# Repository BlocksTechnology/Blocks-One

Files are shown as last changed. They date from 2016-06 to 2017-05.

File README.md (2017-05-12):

# Blocks one
In this repository you will find the firmware source code, BOM, STLs of the printed parts and frames for the [Blocks one 3D printer](http://blockstec.com/one.html)

# Updating the firmware:
 - Download and install Cura 15.02.1: [Win](http://software.ultimaker.com/old/Cura_15.02.1.exe) / [Mac](http://software.ultimaker.com/old/Cura-15.02.1-MacOS.dmg)
 - Download the [HEX file](http://blockstec.com/downloads/Blocks_one_1.2.hex)
 - Connect your USB printer cable
 - Open Cura and select menu "Machine" -> "Install custom firmware"
 - Select the downloaded HEX file.
 - Wait for the upload to finish and press "OK"

In case the update does not start, please verify the "Serial port" and "Baudrate" (250000) settings in the menu "Machine" -> "Machine settings".

# Changelog:
V1.2.1:
 - Homing after print bug solved

V1.2:
 - USB communication bug solved
 - Baudrate changed to 250000

V1.1:
 - New load/unload filament routine
 - Option to clean the nozzle before bed level
 - Thermal runaway safety feature
 - Filament runout (needs printing new extruder and adding a microswitch to work)
 - Reversed direction of the LCD knob

# License
Blocks one is licensed under a [Creative Commons Attribution-ShareAlike 4.0 International License](http://creativecommons.org/licenses/by-sa/4.0/)

# Firmware
The firmware was based on [Marlin](https://github.com/MarlinFirmware/Marlin) and https://github.com/bq/Marlin

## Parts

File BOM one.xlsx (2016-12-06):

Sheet: Blocks One
Item | Quantidade | Dimensões
Acrilico Opalino | 6 | (5mm) 41 x 41cm
Peças Impressas | 20 | zzz
Motores | 4 | Nema 17
Hotend | 1 | zzz
Tira Led | 1 | zzz
Blower | 1 | 50x50x15
Fan | 1 | 30x30x10
Fan | 1 | 50x50x10
Belt GT2 | 3 | 3m
Pulley GT2 | 2 | 6mm
Idler | 8 | 8mm
Fitting | 2 | 4mm
PTFE | 1 | 60cm
Endstop | 3 | 12x6mm
Pinhão Extrusor | 1 | 1.75
Molas Fortes | 2 | zzz
Molas Suaves | 4 | zzz
Varões M8 | 4 | 39cm
Varões M10 | 2 | 39cm
Lead Screw M8 | 1 | 33cm
Rolamento LM8UU | 8 | zzz
Rolamento LM10UU | 4 | zzz
Rolamento 608ZZ | 3 | zzz
Coupling M5/M8 | 1 | zzz
HeatedBed | 1 | zzz
Pwr Supply | 1 | zzz
Arduino Mega 2560 | 1 | zzz
Ramps 1.4 | 1 | zzz
Pololu Drivers | 4 | zzz
LCD Smart Discount | 1 | zzz
Cabo Elect | 1 | zzz
Guia Cabo | 1 | zzz
Int. 220v | 1 | zzz
Cabo Pwr | 1 | zzz
Total

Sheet: REV
Item | QT | Dimensions | Supplier
ACRILIC | 6 | 410x410x5mm
PRINTED PARTS | 35
LEDS STRIP | 1 | 30 mm
BLOWER FAN | 2 |  | http://ledsandchips.com/3DPrinter/Electronics/504
FAN 30X30 | 1 |  | http://ledsandchips.com/3DPrinter/Electronics/470
GT2 BELT | 2 | 125 mm | http://ledsandchips.com/3DPrinter/3DPrinter_Mechanics/328
GT2 PULLEY | 2 |  | http://ledsandchips.com/3DPrinter/3DPrinter_Mechanics/549
IDLER PULLEY | 8 |  | http://ledsandchips.com/3DPrinter/3DPrinter_Mechanics/557
625-2RS Ball Bearing | 16 |  | http://ledsandchips.com/3DPrinter/3DPrinter_Mechanics/550
NICKEL SPACER M5 | 4 | 10mm | http://ledsandchips.com/3DPrinter/3DPrinter_Mechanics/587-2
FITING PTFE | 2 |  | http://ledsandchips.com/3DPrinter/Extruder_HotEnd/463
PTFE TUBE | 1 | 600 mm | http://ledsandchips.com/3DPrinter/Extruder_HotEnd/463
MICROSWITCH | 3 |  | http://ledsandchips.com/080?search=microswitch
MK7 EXTRUDER PIN | 1 |  | http://ledsandchips.com/3DPrinter/Extruder_HotEnd/506
STRONG SPRINGS | 2 | 20mm | https://reprapworld.com/products/mechanical/compression_springs/compression_spring_20mm_od_5mm/
SOFT SPRINGS | 4 | 12mm | http://reprap.pt/pecas/molas
VARÕES M8 | 4 | 380 mm | http://reprap.pt/pecas/varao-liso-ao-metro
VARÔES M10 | 2 | 350 mm | http://reprap.pt/pecas/varao-liso-ao-metro
LEAD SCREW | 1 | 300 mm | http://reprap.pt/pecas/varao-roscado-8mm-dia-por-350mm-comp-com-parafuso
LM8UU | 8 |  | http://ledsandchips.com/3DPrinter/3DPrinter_Mechanics/176
LM10UU | 4 |  | http://ledsandchips.com/3DPrinter/3DPrinter_Mechanics/284
608ZZ Ball Bearing | 1 |  | http://ledsandchips.com/3DPrinter/3DPrinter_Mechanics/368
COUPLING M5/M8 | 1 |  | http://ledsandchips.com/3DPrinter/3DPrinter_Mechanics/299
NEMA17 2.5A | 4 |  | http://ledsandchips.com/Motors/604
HOTEND | 1 |  | Hotend (https://pt.aliexpress.com/item/3D-Printer-E3DV6-Kits-Remote-Long-Distance-Sprinkler-head-Heating-Print-Head-Extruder-Extrusion-head-Heating/32455907727.html)
HEATEDBED | 1 |  | http://www.cubic-print.com/MK3-aluminum
NTC TERMISTOR | 1 |  | http://ledsandchips.com/3DPrinter/Extruder_HotEnd/350
POWER SUPPLY 12v 25A | 1 |  | http://ledsandchips.com/3DPrinter/Electronics/420
ARDUINO MEGA 2560 | 1 |  | http://ledsandchips.com/Arduino/011
RAMPS 1.4 | 1 |  | http://ledsandchips.com/3DPrinter/Electronics/218
POLULO DRIVERS | 4 |  | http://ledsandchips.com/Motors/560
LCD S.DISCOUNT | 1 |  | http://ledsandchips.com/3DPrinter/Electronics/373
CABLE 220V | 1 |  | https://mauser.pt/catalog/product_info.php?cPath=1874_57_331&products_id=76002
CABLE GUIDE | 1 |  | http://www.tme.eu/en/details/cyg-pet-15-bk/polyester-conduits/cyg/cyg-pet15/
POWER PLUG 10A | 1 |  | https://mauser.pt/catalog/product_info.php?cPath=1874_640_1107&products_id=61780
SWITCH 220V | 1 |  | https://mauser.pt/catalog/product_info.php?cPath=324_1401_1402&products_id=66105
GLASS PLATE | 1 | 215x215x3 mm
Screws Nuts & washers
M3 SCREW 10mm | 15
M3 SCREW M3 16mm | 20
M3 SCREW 20mm | 8
M3 SCREW 30mm | 20
M3 SCREW 40mm | 20
M3 SCREW 50mm | 4
M4 SCREW 16mm | 72
M4 SCREW 20mm | 12
M4 SCREW 50mm | 2
M5 SCREW 30mm | 2
M5 SCREW 35mm | 2
M5 SCREW 40mm | 2
M5 SCREW 45mm | 2
M3 NUT | 25
M4 NUT | 120
M5 NUT (SELF TIGHTENING) | 8
M5 WASHER | 8 | 10x1 mm

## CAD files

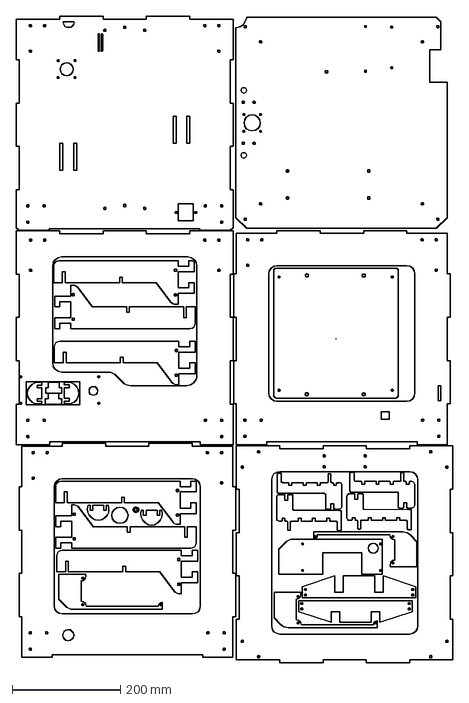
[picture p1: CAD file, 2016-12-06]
frames laser.DXF
806.9 x 1193.1 mm

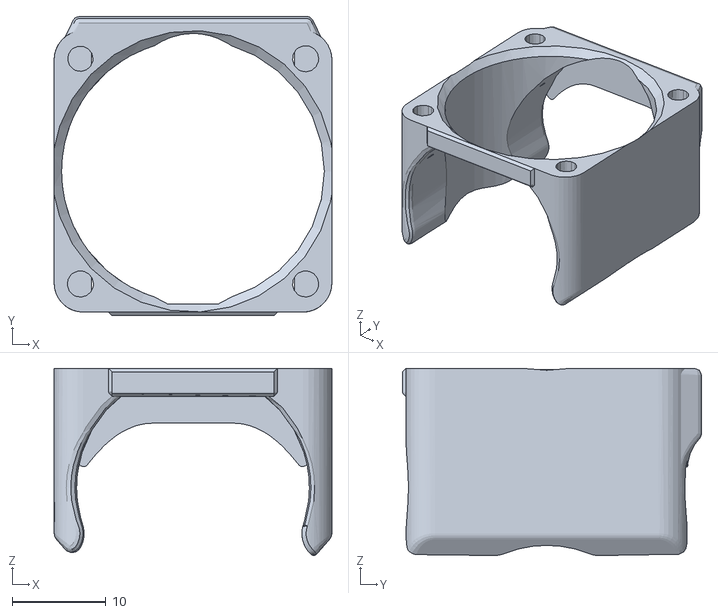
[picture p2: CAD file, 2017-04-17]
STL_Files/1x Fan mount.stl
29.6 x 31.9 x 19.9

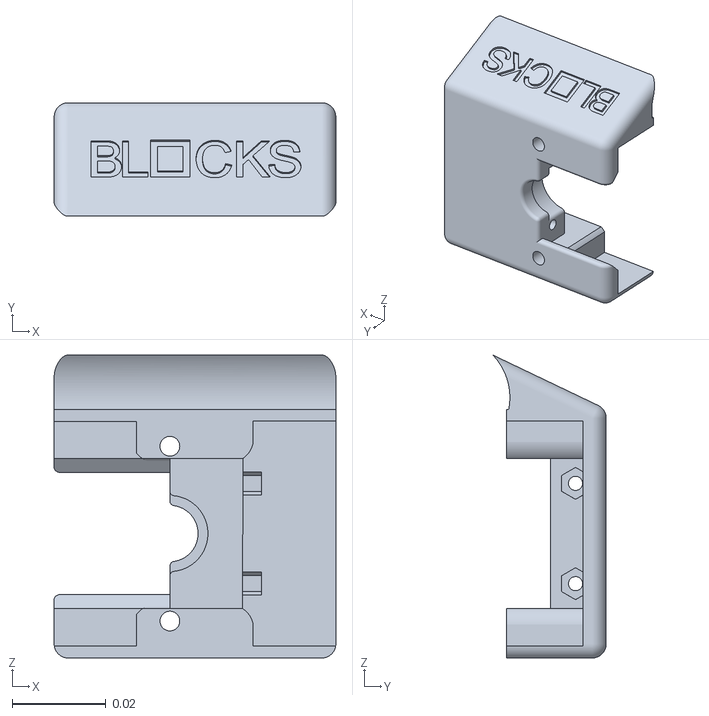
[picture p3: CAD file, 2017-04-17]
STL_Files/1x Hot end mount v2.stl
0.06 x 0.0242 x 0.0645

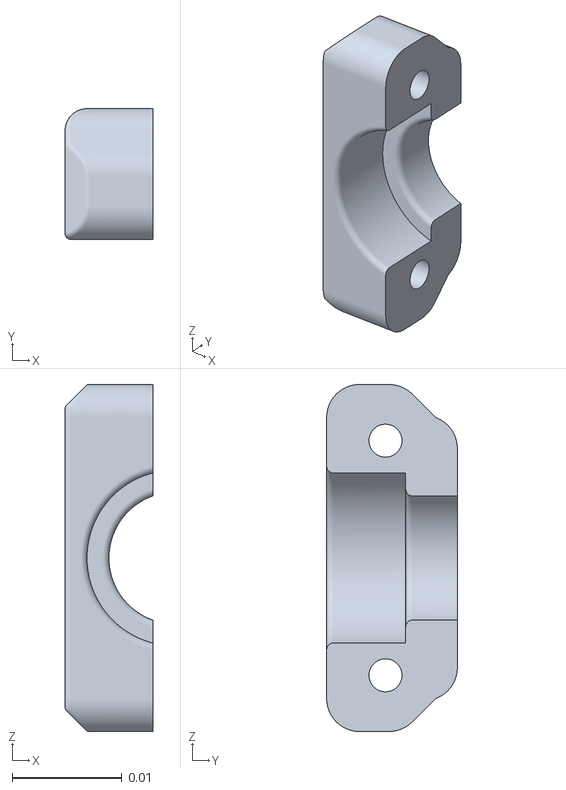
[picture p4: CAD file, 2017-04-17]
STL_Files/1x hot end fixer.stl
0.008 x 0.0119 x 0.0316

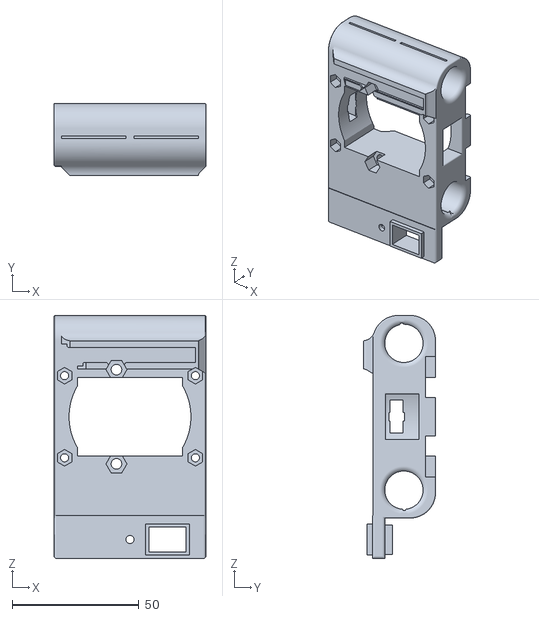
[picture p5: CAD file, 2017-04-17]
STL_Files/1x X carriage.stl
60.0 x 28.5 x 96.0

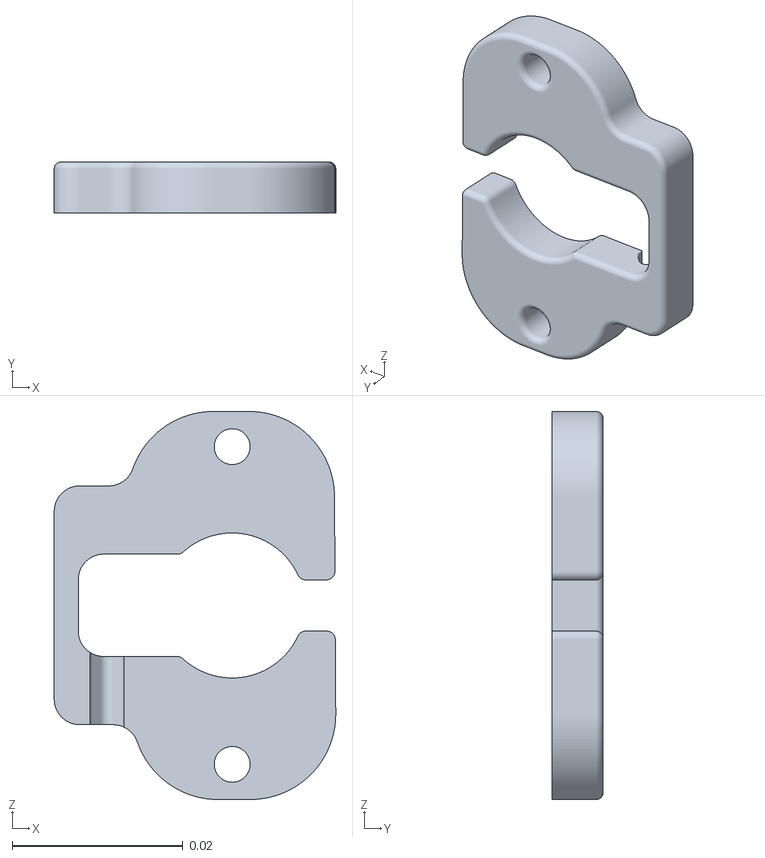
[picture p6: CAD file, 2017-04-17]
STL_Files/1x cable cover.stl
0.033 x 0.006 x 0.0455

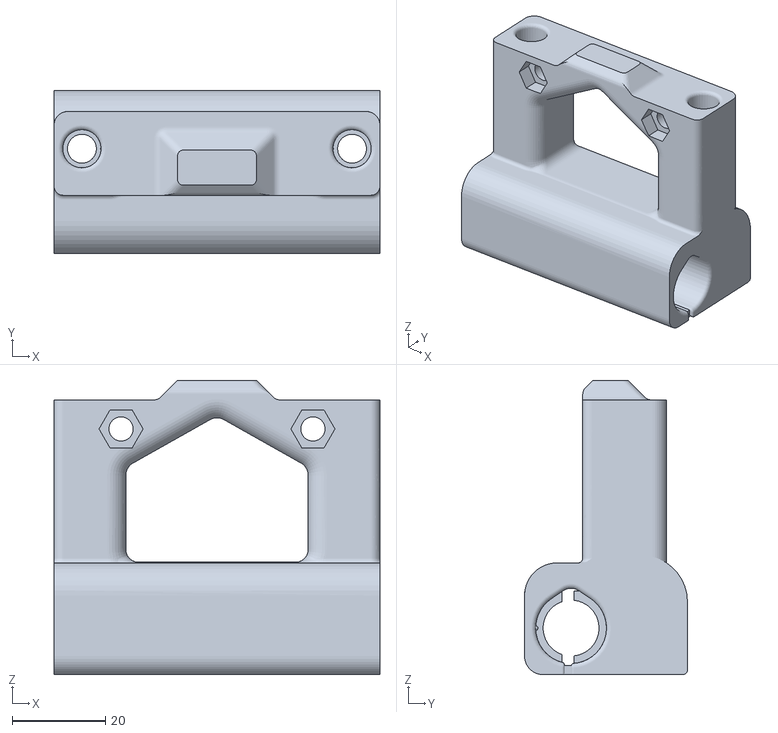
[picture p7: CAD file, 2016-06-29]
STL_Files/1x Carriage Y.STL
70.0 x 35.0 x 63.2

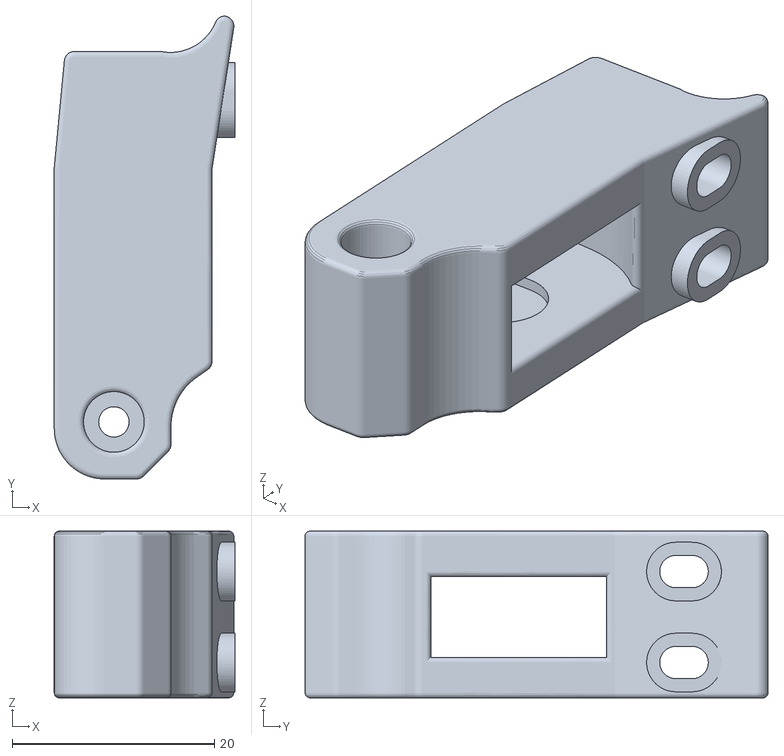
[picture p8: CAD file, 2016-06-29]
STL_Files/1x Extruder idler.stl
17.9 x 45.8 x 16.5

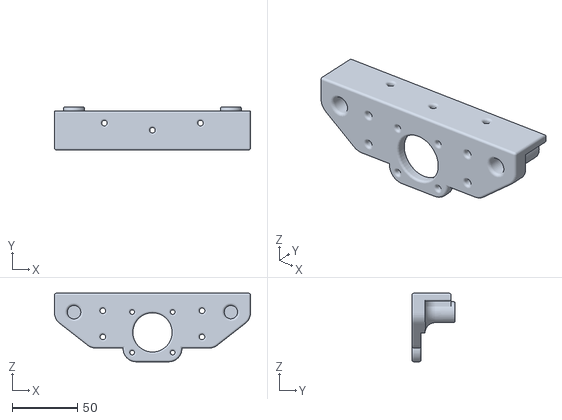
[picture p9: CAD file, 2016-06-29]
STL_Files/1x Z bottom.STL
150.0 x 33.0 x 52.5

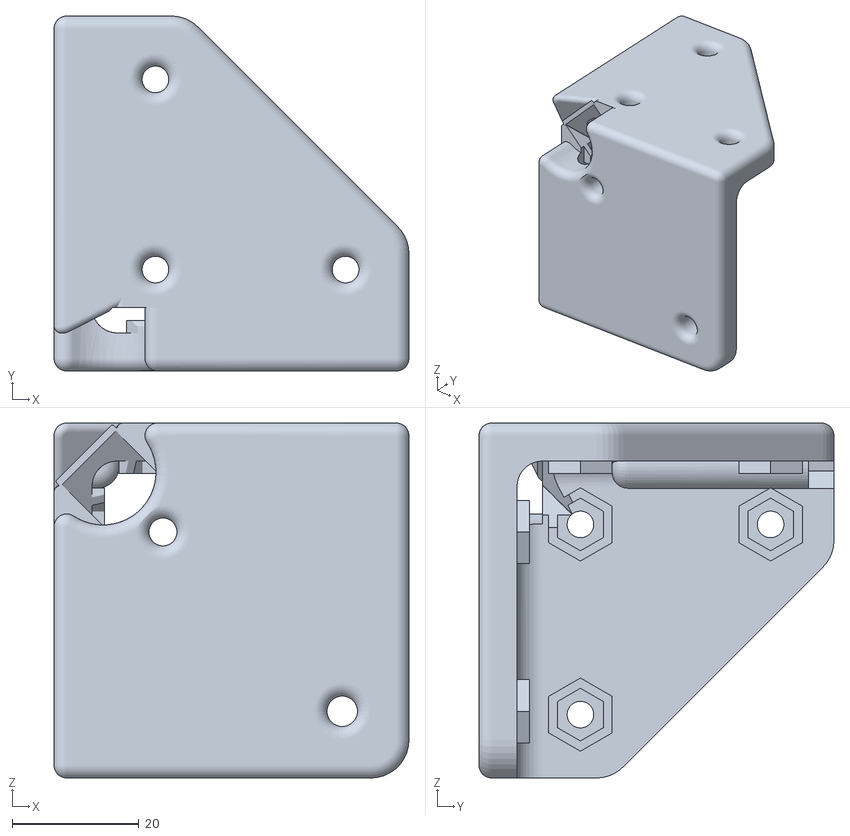
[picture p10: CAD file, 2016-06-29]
STL_Files/4x bottom corner.STL
56.0 x 56.0 x 56.0

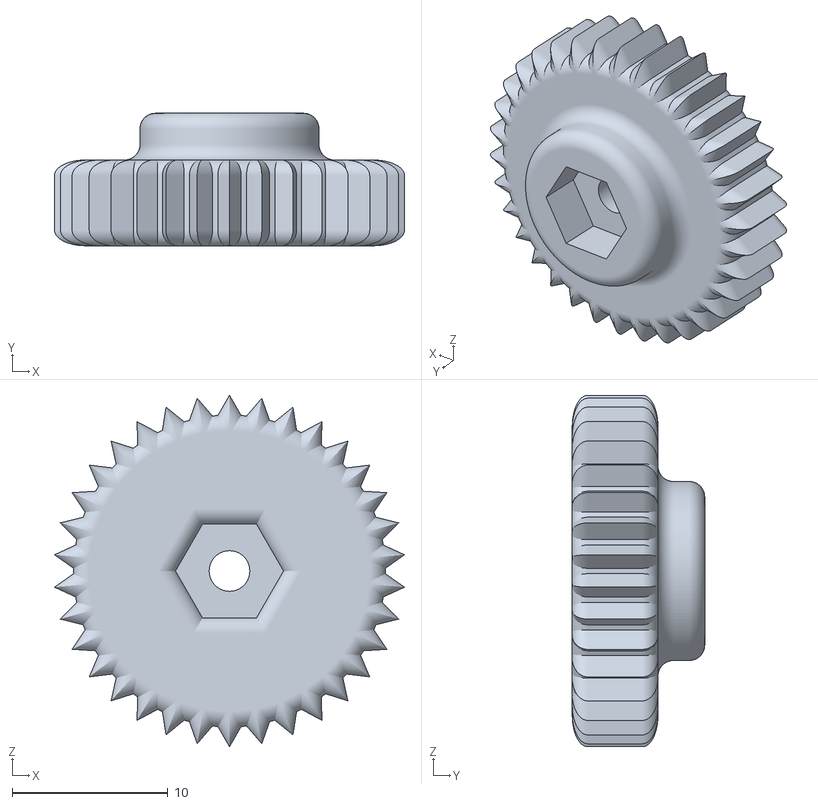
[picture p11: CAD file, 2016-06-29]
STL_Files/4x Plate knob.stl
22.4 x 8.50 x 22.5

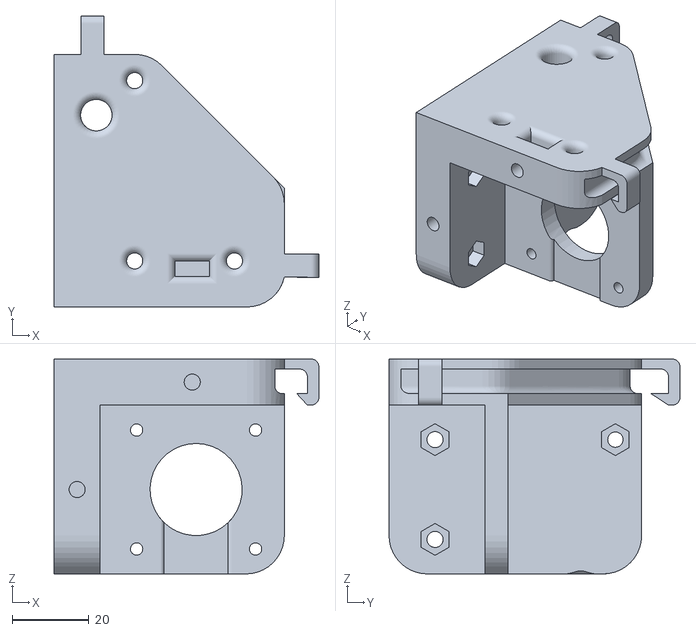
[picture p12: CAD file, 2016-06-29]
STL_Files/1x Motor X corner.STL
69.0 x 75.8 x 56.0

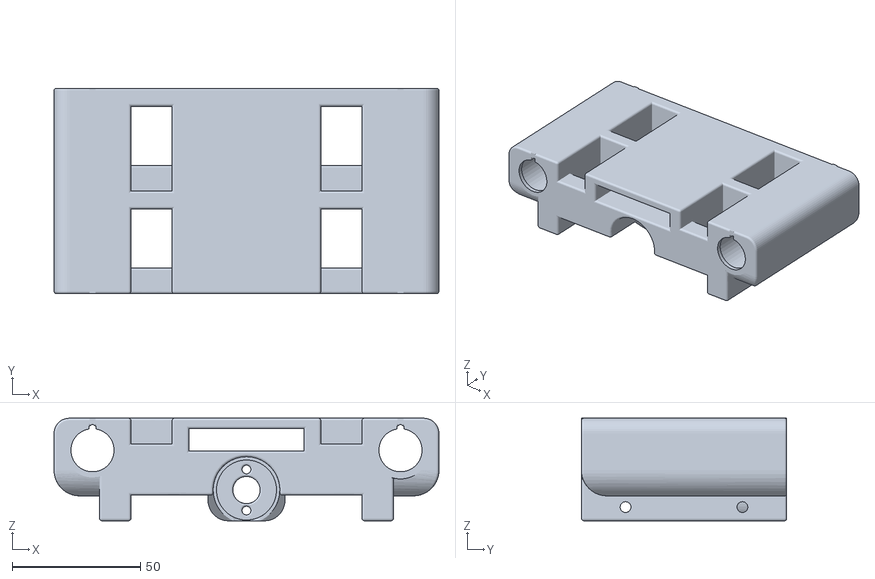
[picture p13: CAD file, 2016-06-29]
STL_Files/1x Z carriage.STL
150.0 x 80.0 x 40.0

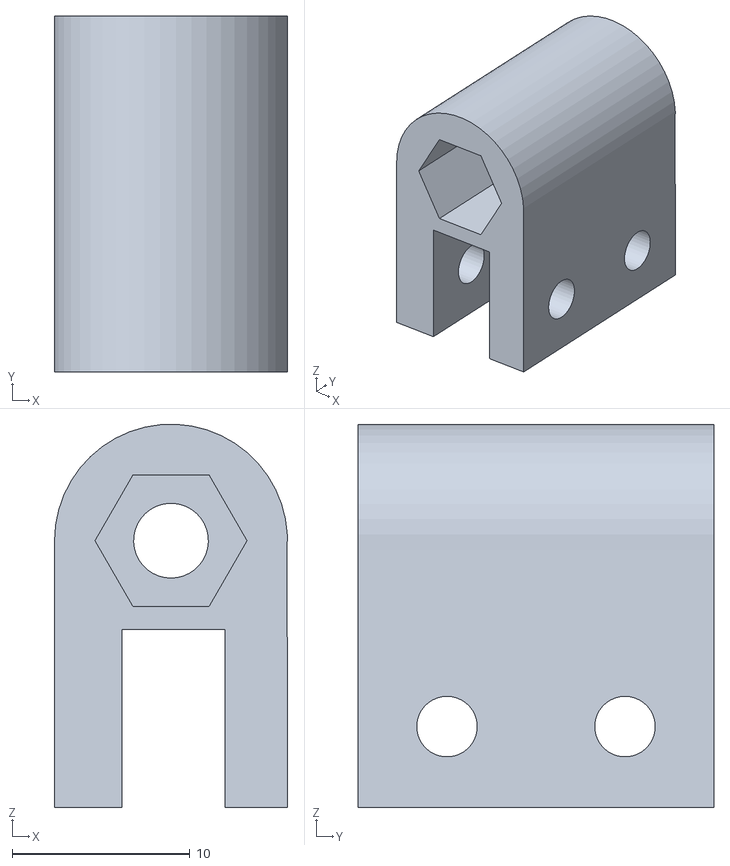
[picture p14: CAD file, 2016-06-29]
STL_Files/4x Plate fixer.STL
13.1 x 20.0 x 21.5

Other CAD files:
STL_Files/1x Corner front right.STL
STL_Files/1x Fan duct.STL
STL_Files/1x Z top.STL
STL_Files/1x Motor Y corner.STL
STL_Files/1x Corner front left.STL

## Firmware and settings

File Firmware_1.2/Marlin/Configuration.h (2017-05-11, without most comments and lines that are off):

#define CONFIGURATION_H
#include "boards.h"
#ifdef USE_AUTOMATIC_VERSIONING
  #include "_Version.h"
#else
  #include "Default_Version.h"
#endif
#define STRING_SPLASH_LINE1 SHORT_BUILD_VERSION // will be shown during bootup in line 1
#define STRING_VERSION_CONFIG_H __DATE__ " " __TIME__ // build date and time
#define STRING_CONFIG_H_AUTHOR "(Blocks, one 1.2.1)" // Who made the changes.
#define SERIAL_PORT 0
#define BAUDRATE 250000
  #define MOTHERBOARD 33
#define EXTRUDERS 1
#define POWER_SUPPLY 1
#define TEMP_SENSOR_0 10
#define TEMP_SENSOR_1 0
#define TEMP_SENSOR_2 0
#define TEMP_SENSOR_BED 1
#define MAX_REDUNDANT_TEMP_SENSOR_DIFF 10
#define TEMP_RESIDENCY_TIME 10  // (seconds)
#define TEMP_HYSTERESIS 3       // (degC) range of +/- temperatures considered "close" to the target one
#define TEMP_WINDOW     1       // (degC) Window around target to start the residency timer x degC early.
#define HEATER_0_MINTEMP 5
#define HEATER_1_MINTEMP 5
#define HEATER_2_MINTEMP 5
#define BED_MINTEMP 5
#define HEATER_0_MAXTEMP 270
#define HEATER_1_MAXTEMP 270
#define HEATER_2_MAXTEMP 270
#define BED_MAXTEMP 110
#define PIDTEMP
#define BANG_MAX 255 // limits current to nozzle while in bang-bang mode; 255=full current
#define PID_MAX BANG_MAX // limits current to nozzle while PID is active (see PID_FUNCTIONAL_RANGE below); 255=full current
  #define PID_FUNCTIONAL_RANGE 10 // If the temperature difference between the target temperature and the actual temperature
  #define PID_INTEGRAL_DRIVE_MAX PID_MAX  //limit for the integral term
  #define K1 0.95 //smoothing factor within the PID
  #define PID_dT ((OVERSAMPLENR * 10.0)/(F_CPU / 64.0 / 256.0)) //sampling period of the temperature routine
    #define  DEFAULT_Kp 22.2
    #define  DEFAULT_Ki 1.08
    #define  DEFAULT_Kd 114
#define MAX_BED_POWER 255 // limits duty cycle to bed; 255=full current
#define PREVENT_DANGEROUS_EXTRUDE
#define EXTRUDE_MINTEMP 170
#define EXTRUDE_MAXLENGTH (X_MAX_LENGTH+Y_MAX_LENGTH) //prevent extrusion of very large distances.
#define THERMAL_RUNAWAY_PROTECTION_PERIOD 40 //in seconds
#define THERMAL_RUNAWAY_PROTECTION_HYSTERESIS 4 // in degree Celsius
#define THERMAL_RUNAWAY_PROTECTION_BED_PERIOD 20 //in seconds
#define THERMAL_RUNAWAY_PROTECTION_BED_HYSTERESIS 2 // in degree Celsius
#define COREXY
#define ENDSTOPPULLUPS // Comment this out (using // at the start of the line) to disable the endstop pullup resistors
  #define ENDSTOPPULLUP_XMAX
  #define ENDSTOPPULLUP_YMAX
  #define ENDSTOPPULLUP_ZMAX
  #define ENDSTOPPULLUP_XMIN
  #define ENDSTOPPULLUP_YMIN
  #define ENDSTOPPULLUP_ZMIN
const bool X_MIN_ENDSTOP_INVERTING = true; // set to true to invert the logic of the endstop.
const bool Y_MIN_ENDSTOP_INVERTING = true; // set to true to invert the logic of the endstop.
const bool Z_MIN_ENDSTOP_INVERTING = true; // set to true to invert the logic of the endstop.
const bool X_MAX_ENDSTOP_INVERTING = true; // set to true to invert the logic of the endstop.
const bool Y_MAX_ENDSTOP_INVERTING = true; // set to true to invert the logic of the endstop.
const bool Z_MAX_ENDSTOP_INVERTING = true; // set to true to invert the logic of the endstop.
#if defined(COREXY) && !defined(DISABLE_MAX_ENDSTOPS)
  #define DISABLE_MAX_ENDSTOPS
#endif
#define X_ENABLE_ON 0
#define Y_ENABLE_ON 0
#define Z_ENABLE_ON 0
#define E_ENABLE_ON 0 // For all extruders
#define DISABLE_X false
#define DISABLE_Y false
#define DISABLE_Z false
#define DISABLE_E false // For all extruders
#define DISABLE_INACTIVE_EXTRUDER true //disable only inactive extruders and keep active extruder enabled
#define INVERT_X_DIR false    // for Mendel set to false, for Orca set to true
#define INVERT_Y_DIR true    // for Mendel set to true, for Orca set to false
#define INVERT_Z_DIR true     // for Mendel set to false, for Orca set to true
#define INVERT_E0_DIR false   // for direct drive extruder v9 set to true, for geared extruder set to false
#define INVERT_E1_DIR false    // for direct drive extruder v9 set to true, for geared extruder set to false
#define INVERT_E2_DIR false   // for direct drive extruder v9 set to true, for geared extruder set to false
#define X_HOME_DIR -1
#define Y_HOME_DIR -1
#define Z_HOME_DIR -1
#define min_software_endstops true // If true, axis won't move to coordinates less than HOME_POS.
#define max_software_endstops true  // If true, axis won't move to coordinates greater than the defined lengths below.
#define X_MAX_POS 200
#define X_MIN_POS 0
#define Y_MAX_POS 200
#define Y_MIN_POS 0
#define Z_MAX_POS 200
#define Z_MIN_POS 0
#define X_MAX_LENGTH (X_MAX_POS - X_MIN_POS)
#define Y_MAX_LENGTH (Y_MAX_POS - Y_MIN_POS)
#define Z_MAX_LENGTH (Z_MAX_POS - Z_MIN_POS)
#define Z_PROBE_REPEATABILITY_TEST  // If not commented out, Z-Probe Repeatability test will be included if Auto Bed Leveling is Enabled.
#define MANUAL_X_HOME_POS 0
#define MANUAL_Y_HOME_POS 0
#define MANUAL_Z_HOME_POS 0
#define NUM_AXIS 4 // The axis order in all axis related arrays is X, Y, Z, E
#define HOMING_FEEDRATE {2000, 2000, 1000, 0}  //{50*60, 50*60, 4*60, 0} set the homing speeds (mm/min)
#define DEFAULT_AXIS_STEPS_PER_UNIT   {80, 80, 400,97}  // default steps per unit for Ultimaker
#define DEFAULT_MAX_FEEDRATE          {250, 250, 10, 80}    // (mm/sec)
#define DEFAULT_MAX_ACCELERATION      {3000,3000,100,10000}    // X, Y, Z, E maximum start speed for accelerated moves. E default values are good for Skeinforge 40+, for older versions raise them a lot.
#define DEFAULT_ACCELERATION          2000    // X, Y, Z and E max acceleration in mm/s^2 for printing moves
#define DEFAULT_RETRACT_ACCELERATION  1000   // X, Y, Z and E max acceleration in mm/s^2 for retracts
#define DEFAULT_XYJERK                20.0    // (mm/sec)
#define DEFAULT_ZJERK                 0.4     // (mm/sec)
#define DEFAULT_EJERK                 5.0    // (mm/sec)
#define CUSTOM_M_CODES
  #define CUSTOM_M_CODE_SET_Z_PROBE_OFFSET 851
  #define Z_PROBE_OFFSET_RANGE_MIN -15
  #define Z_PROBE_OFFSET_RANGE_MAX 0
#define FILAMENT_RUNOUT_SENSOR
#define FIL_RUNOUT_PIN 4
#define FIL_RUNOUT_INVERTING false
#define EXTRUSION_SPEED 200
#define LEVEL_PLATE_TEMP_PROTECTION 60
#define Change_Filament_Target_Temp 220
#define FILAMENT_EXTRUSION_LENGTH 30
#define FILAMENT_UNLOAD_EXTRUSION_LENGTH 5
#define FILAMENT_UNLOAD_RETRACTION_LENGTH 700
#define PREHEAT_HOTEND_TEMP 180
#define PREHEAT_FAN_SPEED 0
#define COOLDOWN_FAN_SPEED 255
#define XY_TRAVEL_SPEED 8000    // X and Y axis travel speed between probes and Witbox movements, in mm/min
#define EEPROM_SETTINGS
#define PLA_PREHEAT_HOTEND_TEMP 180
#define PLA_PREHEAT_HPB_TEMP 70
#define PLA_PREHEAT_FAN_SPEED 255   // Insert Value between 0 and 255
#define ABS_PREHEAT_HOTEND_TEMP 240
#define ABS_PREHEAT_HPB_TEMP 100
#define ABS_PREHEAT_FAN_SPEED 255   // Insert Value between 0 and 255
#define SDSUPPORT // Enable SD Card Support in Hardware Console
#define REPRAP_DISCOUNT_SMART_CONTROLLER
 #define ULTIPANEL
 #define NEWPANEL
  #define SDSUPPORT
  #define ULTRA_LCD
    #define LCD_WIDTH 20
    #define LCD_HEIGHT 4
#define SOFT_PWM_SCALE 0
#define NUM_SERVOS 1 // Servo index starts with 0 for M280 command
#define SERVO_ENDSTOPS {-1, -1, 0} // Servo index for X, Y, Z. Disable with -1
#define SERVO_ENDSTOP_ANGLES {0,0, 0,0, 10,90} // X,Y,Z Axis Extend and Retract angles
#define FILAMENT_SENSOR_EXTRUDER_NUM	0  //The number of the extruder that has the filament sensor (0,1,2)
#define MEASUREMENT_DELAY_CM			14  //measurement delay in cm.  This is the distance from filament sensor to middle of barrel
#define DEFAULT_NOMINAL_FILAMENT_DIA  3.0  //Enter the diameter (in mm) of the filament generally used (3.0 mm or 1.75 mm) - this is then used in the slicer software.  Used for sensor reading validation
#define MEASURED_UPPER_LIMIT          3.30  //upper limit factor used for sensor reading validation in mm
#define MEASURED_LOWER_LIMIT          1.90  //lower limit factor for sensor reading validation in mm
#define MAX_MEASUREMENT_DELAY			20  //delay buffer size in bytes (1 byte = 1cm)- limits maximum measurement delay allowable (must be larger than MEASUREMENT_DELAY_CM  and lower number saves RAM)
#define DEFAULT_MEASURED_FILAMENT_DIA  DEFAULT_NOMINAL_FILAMENT_DIA  //set measured to nominal initially
#include "Configuration_adv.h"
#include "thermistortables.h"

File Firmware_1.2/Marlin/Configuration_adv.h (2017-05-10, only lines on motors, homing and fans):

#define CONTROLLERFAN_PIN -1 //Pin used for the fan to cool controller (-1 to disable)
#define EXTRUDER_0_AUTO_FAN_PIN   -1
#define EXTRUDER_1_AUTO_FAN_PIN   -1
#define EXTRUDER_2_AUTO_FAN_PIN   -1
#define X_HOME_RETRACT_MM 5
#define Y_HOME_RETRACT_MM 5
#define Z_HOME_RETRACT_MM 3
#define MICROSTEP1 LOW,LOW
#define MICROSTEP2 HIGH,LOW
#define MICROSTEP4 LOW,HIGH
#define MICROSTEP8 HIGH,HIGH
#define MICROSTEP16 HIGH,HIGH
#define MICROSTEP_MODES {16,16,16,16,16} // [1,2,4,8,16]
#define DIGIPOT_MOTOR_CURRENT {135,135,135,135,135} // Values 0-255 (RAMBO 135 = ~0.75A, 185 = ~1A)
#define DIGIPOT_I2C_MOTOR_CURRENTS {1.0, 1.0, 1.0, 1.0, 1.0, 1.0, 1.0, 1.0}

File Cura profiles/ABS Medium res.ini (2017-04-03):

[profile]
layer_height = 0.16
wall_thickness = 1.2
retraction_enable = True
solid_layer_thickness = 1
fill_density = 20
nozzle_size = 0.4
print_speed = 45
print_temperature = 260
print_temperature2 = 0
print_temperature3 = 0
print_temperature4 = 0
print_temperature5 = 0
print_bed_temperature = 90
support = None
platform_adhesion = Brim
support_dual_extrusion = Both
wipe_tower = False
wipe_tower_volume = 15
ooze_shield = False
filament_diameter = 1.75
filament_diameter2 = 0
filament_diameter3 = 0
filament_diameter4 = 0
filament_diameter5 = 0
filament_flow = 102.0
retraction_speed = 45
retraction_amount = 5.5
retraction_dual_amount = 16.5
retraction_min_travel = 1.5
retraction_combing = All
retraction_minimal_extrusion = 0.02
retraction_hop = 0.0
bottom_thickness = 0.3
layer0_width_factor = 100
object_sink = 0.0
overlap_dual = 0.15
travel_speed = 150.0
bottom_layer_speed = 20
infill_speed = 0.0
solidarea_speed = 0.0
inset0_speed = 0.0
insetx_speed = 0.0
cool_min_layer_time = 5
fan_enabled = True
skirt_line_count = 1
skirt_gap = 3.0
skirt_minimal_length = 150.0
fan_full_height = 0.5
fan_speed = 30
fan_speed_max = 45
cool_min_feedrate = 10
cool_head_lift = False
solid_top = True
solid_bottom = True
fill_overlap = 15
support_type = Lines
support_angle = 60
support_fill_rate = 15
support_xy_distance = 0.7
support_z_distance = 0.15
spiralize = False
simple_mode = False
brim_line_count = 20
raft_margin = 5.0
raft_line_spacing = 3.0
raft_base_thickness = 0.3
raft_base_linewidth = 1.0
raft_interface_thickness = 0.27
raft_interface_linewidth = 0.4
raft_airgap_all = 0.0
raft_airgap = 0.22
raft_surface_layers = 2
raft_surface_thickness = 0.27
raft_surface_linewidth = 0.4
fix_horrible_union_all_type_a = True
fix_horrible_union_all_type_b = False
fix_horrible_use_open_bits = False
fix_horrible_extensive_stitching = False
plugin_config = 
object_center_x = -1
object_center_y = -1

[alterations]
start.gcode = ;Sliced at: {day} {date} {time}
	;Basic settings: Layer height: {layer_height} Walls: {wall_thickness} Fill: {fill_density}
	;Print time: {print_time}
	;Filament used: {filament_amount}m {filament_weight}g
	;Filament cost: {filament_cost}
	;M190 S{print_bed_temperature} ;Uncomment to add your own bed temperature line
	;M109 S{print_temperature} ;Uncomment to add your own temperature line
	G21        ;metric values
	G90        ;absolute positioning
	M82        ;set extruder to absolute mode
	M107       ;start with the fan off
	G28 X0 Y0  ;move X/Y to min endstops
	G28 Z0     ;move Z to min endstops
	G1 Z15.0 F{travel_speed} ;move the platform down 15mm
	G92 E0                  ;zero the extruded length
	G1 F200 E3              ;extrude 3mm of feed stock
	G92 E0                  ;zero the extruded length again
	G1 F{travel_speed}
	;Put printing message on LCD screen
	M117 Printing...
end.gcode = ;End GCode
	M104 S0                     ;extruder heater off
	M140 S0                     ;heated bed heater off (if you have it)
	G91                                    ;relative positioning
	G1 E-1 F300                            ;retract the filament a bit before lifting the nozzle, to release some of the pressure
	G1 Z+0.5 E-5 X-20 Y-20 F{travel_speed} ;move Z up a bit and retract filament even more
	G28 X0 Y0                              ;move X/Y to min endstops, so the head is out of the way
	M84                         ;steppers off
	G90                         ;absolute positioning
	;{profile_string}
start2.gcode = ;Sliced at: {day} {date} {time}
	;Basic settings: Layer height: {layer_height} Walls: {wall_thickness} Fill: {fill_density}
	;Print time: {print_time}
	;Filament used: {filament_amount}m {filament_weight}g
	;Filament cost: {filament_cost}
	;M190 S{print_bed_temperature} ;Uncomment to add your own bed temperature line
	;M104 S{print_temperature} ;Uncomment to add your own temperature line
	;M109 T1 S{print_temperature2} ;Uncomment to add your own temperature line
	;M109 T0 S{print_temperature} ;Uncomment to add your own temperature line
	G21        ;metric values
	G90        ;absolute positioning
	M107       ;start with the fan off
	G28 X0 Y0  ;move X/Y to min endstops
	G28 Z0     ;move Z to min endstops
	G1 Z15.0 F{travel_speed} ;move the platform down 15mm
	T1                      ;Switch to the 2nd extruder
	G92 E0                  ;zero the extruded length
	G1 F200 E10             ;extrude 10mm of feed stock
	G92 E0                  ;zero the extruded length again
	G1 F200 E-{retraction_dual_amount}
	T0                      ;Switch to the first extruder
	G92 E0                  ;zero the extruded length
	G1 F200 E10             ;extrude 10mm of feed stock
	G92 E0                  ;zero the extruded length again
	G1 F{travel_speed}
	;Put printing message on LCD screen
	M117 Printing...
end2.gcode = ;End GCode
	M104 T0 S0                     ;extruder heater off
	M104 T1 S0                     ;extruder heater off
	M140 S0                     ;heated bed heater off (if you have it)
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

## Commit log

2015-06-24 Added DXF file for frame cutting
    [Frames.dxf]
2015-07-12 Minor tweaks
    Changed: Max temp, change filament speed, added bed temp and fan control
    furing print, extruder steps 97, fan speed restricted to 60%
    [Configuration.h, X carriage.stl, Y carriage x2.stl]
2015-08-13 Inverting endstop corrected
    [Configuration.h]
2015-09-16 Extruder disable timeout removed
    [Configuration_adv.h]
2016-04-13 Tweaks
    Increase of maximum temperature.
    Fixed "Stop print" bug.
    [Configuration.h]
2016-06-20 Max fan speed removed
    Removes the limit of 130 speed of the nozzle cooling fan
2016-06-29 Printed parts update
    Update of the STL models.
    [Carriage Y.STL, Carril de X.stl, Corner bottom x4.stl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]
2016-06-29 Cura profiles added
    Cura profiles added for PLA, ABS, FLEX and PETG filaments.
2016-12-06 BOM & Frames
    [BOM one.xlsx, frames laser.DXF]
2017-04-03 Cura profiles
    Addition of the cura print profiles
2017-04-17 Firmware 1.1
    new features:
    -new load/unload filament routine
    -nozzle clean before bed level
    -thermal runaway
    -filament runout
    [1x Carriage Y.STL, 1x Corner front left.STL, 1x Corner front right.STL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]
2017-04-21 Debugging verbose removed
    removed serial port prints for debugging thermal runaway
2017-05-03 Firmware 1.2
    [Configuration.h, Configuration_adv.h, Menu Plans.xlsx]
2017-05-10 Firmware 1.2.1
    Homing after print bug solved
    [Configuration.h, Configuration_adv.h]
2017-05-10 Firmware 1.2.1
    Correct version display boot screen
    [Configuration.h]
2017-05-10 Firmware 1.2.1
    [Configuration.h]
